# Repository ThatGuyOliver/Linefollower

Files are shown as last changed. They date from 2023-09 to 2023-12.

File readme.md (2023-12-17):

# LineFollower

A description of my image


## specifications

microcontroller:AZ-Delivery ESP32-WROOM-32

motors: Mini Micro Metal Gear Motor 6V 500TPM

h-bridge:Drv8833

sensors:QTR-8A

batteries:XTAR 2200mAh Li-ion battery

wireless communication: AZ-Delivery ESP32-WROOM-32

distance sensor - motors: 8,57 cm

weight: 260g

speed: 0.774 m/s

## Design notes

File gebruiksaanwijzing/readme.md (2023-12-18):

# Gebruiksaanwijzing

## opladen / vervangen batterijen
uitleg over het opladen of vervangen van de batterijen

### Opladen
Dit zijn li-ion batterijen van het type 18650.
Deze batterijen laad je best op voor en na een sessie.
Wanneer tijdens een sessie een verminderde prestatie wordt geleverd kan je dan ook best de batterijen opladen.
Voor het opladen van deze batterijen heb je een speciale lader nodig en wordt het ten zeerste afgeraden om een niet geschikte oplaadmethode te gebruiken.

### Vervangen batterijen
Zorg dat de batterijen in de correcte oriëntatie in de batterijhouder gestoken worden. En vergeet het deksel niet terug te plaatsen
Er wordt ook zeker aangeraden dat wanneer je deze batterijen vervangt, je ze afgeeft bij een geschikt inzamelings punt.

## draadloze communicatie
### verbinding maken
uitleg over het verbinden van de robot met laptop / smartphone
#### 1: Putty (op computer)
1.Verbind met hetzelde Wifi netwerk als de esp32
1.1. Het netwerk waarmee de esp32 wordt bepaald wordt bepaald in de main.cpp file.
2. Hostname: zelf gekozen hostname/ip esp32
2.1 Hostname wordt gekozen in main.cpp file
3. Port:  23
4. Connection type: Other: Telnet
#### 2: App IOS Termius
1.Verbind met hetzelde Wifi netwerk als de esp32
2. Navigeer naar Hosts tab
3. Klik op + in de linker hoek
4. New host
5. Hostname 
5.1 Hostname: zelf gekozen hostname 
6. Schakel Use SSH uit
7. Schakel Use Telnet aan
8. Save 
9. Klik nu op de net aangemaakte host

### commando's
#### debug Stuurt alle ingestelde parameters en berekende calculation time terug.
#### run Start of stopt de robot.
#### set cycle [µs]  Stelt de cycle time in van de robot.
#### set power [0..255] Stelt de maximum power van de robot in.
#### set diff [0..1] Stelt de verschil in power tussen de motoren in bochten
#### set kp [0..] Stelt de propertionele correctie van de fout in.
#### set ki [0..] Stelt de integrale correctie van de fout in.
#### set kd [0..] Stelt de differentiële correctie van de fout in.
#### calibrate black  Stelt de waardes gelezen door de sensor in als zwart.
#### calibrate white Stelt de waardes gelezen door de sensor in als wit.

## kalibratie
uitleg kalibratie  
Er moet worden gekalibreerd omdat er een verschil is tussen de verschillende sensoren, door een tolerantie op de onderdelen, wat eigen is aan productie.

Commando: calibrate black
Wanneer je dit commando stuurt over telnet wordt de reflectie van het opppervlakte waarover de sensor module op dat moment hangt opgeslagen
per sensor opgeslagen als een zwart waarde.
Commando: calibrate white
Wanneer je dit commando stuurt over telnet wordt de reflectie van het opppervlakte waarover de sensor module op dat moment hangt opgeslagen
per sensor opgeslagen als een wit waarde.

Deze waardes worden dan gebruikt om te vergelijken met de huidig gedetecteerd oppervlakte ofdat het een wit of zwart oppervlakte is.
Het is belangrijk dat je deze commandos opnieuw uitvoerd wanneer je van omgeving verandert zodat er correct kan gedetecteerd kan worden.

## settings
De robot rijdt stabiel met volgende parameters:  
#### cycle time: 2500
#### power: 80
#### Diff: 0.10
#### Kp: 30
#### Ki: 0
#### Kd: 1.00

## settings optimaal Plan A
#### cycle time: 200
#### power: 200
#### Diff: 0.01
#### Kp: 10
#### Ki: 0
#### Kd: 0.8

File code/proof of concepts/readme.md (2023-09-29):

# Proof of Concepts

Een proof of concept is een combinatie van minimale hard- en software om eenvoudig aan te tonen dat iets werkt.  
Proof of concepts kunnen enerzijds als eerste poging dienen om een bepaald onderdeel van het project werkend te krijgen. Anderzijds kunnen ze tijdens het debuggen van het finale project dienen als test om eventuele hardware problemen te elimineren bij onduidelijke problemen.
<br />  
<br />
Een proof of concept bestaat uit
* een elektronisch schema (indien van toepassing)
* minimale code om de voorop gestelde zaken te demonstreren
* minimale uitleg / aandachtspunten
<br />
De elektronische schakelingen van de proof of concepts komen bij voorkeur overeen met deze van de uiteindelijke linefollower, zodat de code zonder aanpassingen op het finale project kan draaien.

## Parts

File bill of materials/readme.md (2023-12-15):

## bill of materials plan B
<br />

|volgnummer|naam|omschrijving|nieuw/recup|kostprijs/stuk[€]|aantal|subtotaal[€]|
|---|----|---|---|---|---|---|
|1| Drv8833 H-Brug | Aliexpress 3-10V H-Brug | nieuw | 3,57|1|3,57|
|2|Breadboard| Aliexpress 400mm punten| nieuw|1,02|2|2,04|
|3|DC Motor| 6V DC, 50:1 ratio| nieuw | 2,04|2 |4,08|
|4|Achter Wiel| 40mm rubber wiel|nieuw|0,79|2|1,58|
|5|Batterij Houder| 2x18650 Batterij met switch|nieuw|0,32|1|0,32|
|6|Lijmpistool en patroon | HBM met 2 patronen | recup|2,99 | 1 |2,99|
|7|Reflectance sensor array |Polollulu QTR-8A|nieuw|10,39|1|10,39|
|7|Batterij lader|XTAR MC2 Plus batterijlader|nieuw|6,95|1|6,95|
|9|Batterij|XTAR 18650 2200mAh (protected) 5A|nieuw|4,45|2|8,90|
|10|ESP32 Microcontroller|AZ-Delivery ESP32-WROOM-32 NodeMCU Module|nieuw|7,60|1|7,60|
|11|Kabels|Meerkleurige kabels 0,75mm|nieuw|7|1|7|
|12|Voltage Regulator| +5V 1,5A L7805CV|0,75|1|0,75|
|13|Kogelwiel| Draaiende bal voor voorwiel|nieuw|1,10|1|1,10|
|14|Verbindings kabel| Micro USB voor connector ESP32|recup|*|1|*|
|15|Baseplate|Plaat waarop alles bevestigd wordt|nieuw|0,47|1|0,47|
|16|Motorhouders|Polulu motor houder|nieuw|0,06|2|0,12|
|17|Batterij Houder Platform| Verhoog voor montering battery houder|nieuw|0,58|1|0,58|
|18|Schroef|M3x12|recup|0,10|4|0,40|
|19|Moer|M3|recup|0,10|4|0,40|

## bill of materials plan A
<br />

|volgnummer|naam|omschrijving|nieuw/recup|kostprijs/stuk[€]|aantal|subtotaal[€]|
|---|----|---|---|---|---|---|
|1| Drv8833 H-Brug | Aliexpress 3-10V H-Brug | nieuw | 3,57|1|3,57|
|2|PCB Mainboard|Vervanging van breadboard|nieuw|2,63|1|2,63|
|3|DC Motor| 6V DC, 50:1 ratio| nieuw | 2,04|2 |4,08|
|4|Achter Wiel| 40mm rubber wiel|nieuw|0,79|2|1,58|
|5|Batterij Houder| 2x18650 Batterij met switch|nieuw|0,32|1|0,32|
|6|Lijmpistool en patroon | HBM met 2 patronen | recup|2,99 | 1 |2,99|
|7|Reflectance sensor array |Polollulu QTR-8A|nieuw|10,39|1|10,39|
|7|Batterij lader|XTAR MC2 Plus batterijlader|nieuw|6,95|1|6,95|
|9|Batterij|XTAR 18650 2200mAh (protected) 5A|nieuw|4,45|2|8,90|
|10|ESP32 Microcontroller|AZ-Delivery ESP32-WROOM-32 NodeMCU Module|nieuw|7,60|1|7,60|
|11|Kabels|Meerkleurige kabels 0,75mm|nieuw|7,00|1|7,00|
|12|Voltage Regulator| +5V 1,5A L7805CV|0,75|1|0,75|
|13|Kogelwiel| Draaiende bal voor voorwiel|nieuw|1,10|1|1,10|
|14|Verbindings kabel| Micro USB voor connector ESP32|recup|*|1|*|
|15|Baseplate|Plaat waarop alles bevestigd wordt|nieuw|0,47|1|0,47|
|16|Motorhouders|Polulu motor houder|nieuw|0,06|2|0,12|
|17|Batterij Houder Platform| Verhoog voor montering battery houder|nieuw|0,58|1|0,58|
|18|3 pin header f |Connector U-regulator|nieuw|0,12|1|0,12|
|19|20 pin header f| Connector esp32|nieuw|0,36|2|0,72|
|20|6 pin header f|Connector Drv8833 H-Brug|nieuw|0,18|2|0,36|
|21|12 pin header f|Connector Sensor|nieuw|0,28|1|0,28|
|22|4 pin Terminal Block| Terminal Block connector voor motoren|nieuw|0,45|1|0,45|
|23|2 pin Terminal Block| Terminal Block connector voor batterijen|nieuw|0,30|1|0,30|
|24|Schroef|M3x12|recup|0,10|4|0,40|
|25|Moer|M3|recup|0,10|4|0,40|

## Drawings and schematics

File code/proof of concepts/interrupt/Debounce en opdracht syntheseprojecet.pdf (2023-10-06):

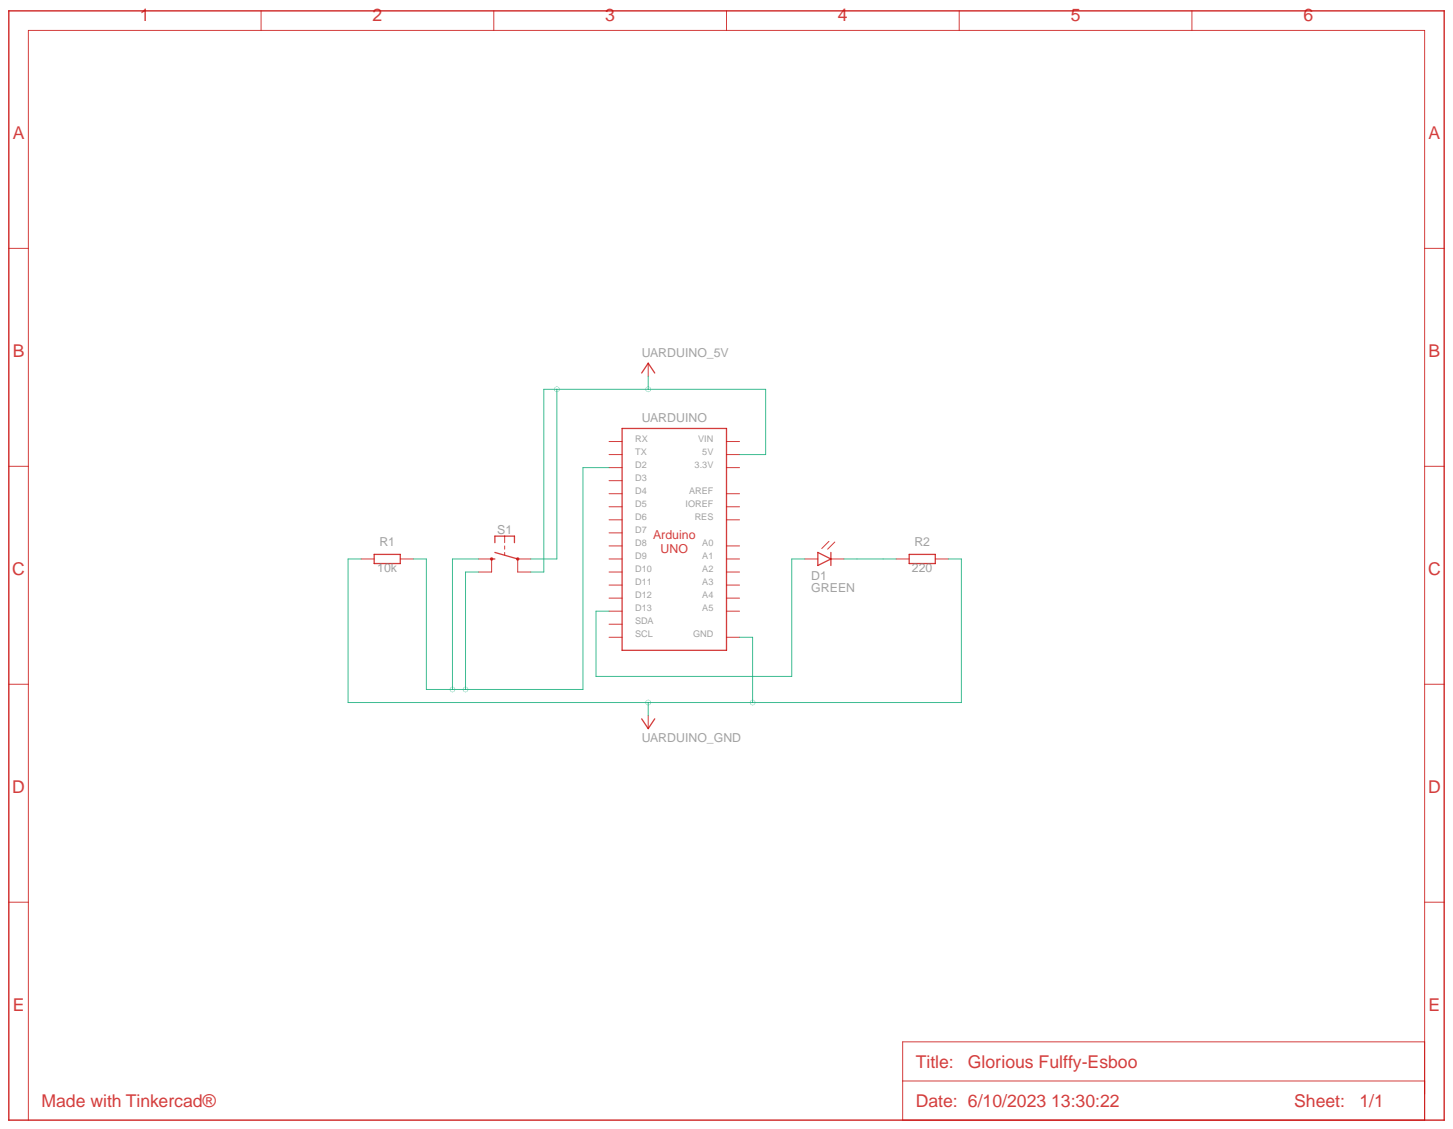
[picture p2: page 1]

Title: Glorious Fulffy-Esboo

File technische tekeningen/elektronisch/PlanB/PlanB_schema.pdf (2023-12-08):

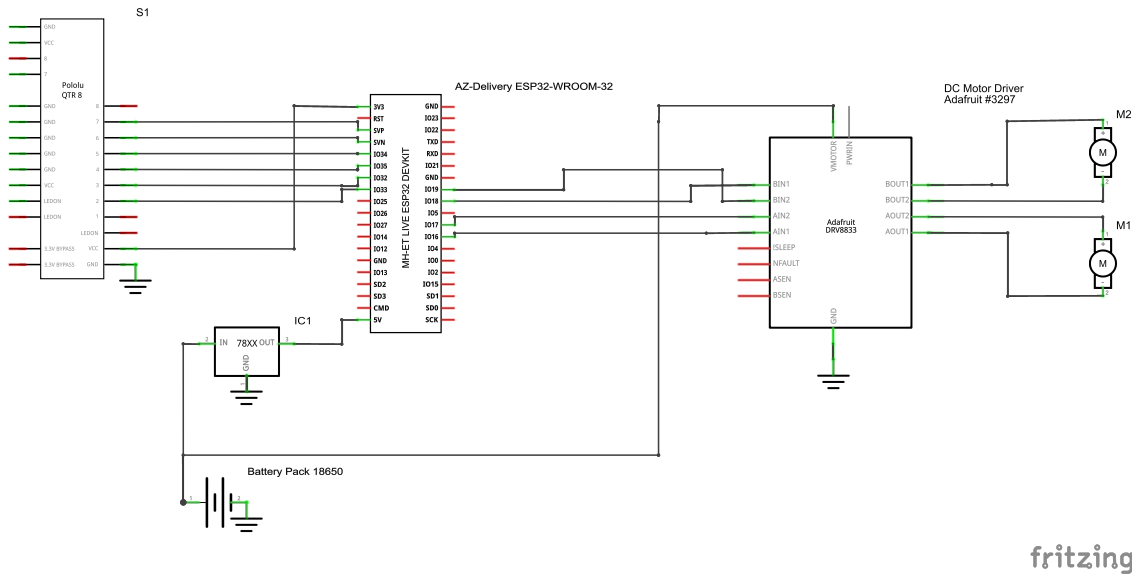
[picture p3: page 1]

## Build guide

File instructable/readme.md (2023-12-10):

# Instructable voor plan B

Een instructable is een stappenplan - zonder verdere uitleg - hoe je vertrekkend van de bill of materials en gebruik makend van de technische tekeningen de robot kan nabouwen. Ook de nodige stappen om de microcontroller te compileren en te uploaden staan beschreven.  

## stap 1
Bestel alle componenten uit de bill of materials  
## stap 2
Leg de breadboards in de lengte naast elkaar.
## stap 3
Maak de zijstukken los, maar behoud één zijstuk op één breadboard.
## stap 4
Nu moet je een configuratie verkrijgen van breadboards zoals volgt: Groot Breadboard - Klein Breadboard - Groot Breadboard. Hang deze breadboards aan elkaar.
## stap 5
Verwijder de gele sticker aan de onderkant van het breadboard, zodat de onderkant plakkerig wordt.
## stap 6
Plak dit breadboard nu op de baseplate tussen de verhogingen en vlak met de achterkant van de baseplate (Niet bij de uitsteeksels).
## stap 7
Knip de uitsteeksels af totdat er nog 4 gaten overblijven op elk uitsteeksel.
## stap 8
Soldeer de draadjes aan de motoren (eventueel knip je een draad in twee).
## stap 9
Lijm de motorhouders nu vast zodat de palmbomen naar buiten wijzen en ze in hun respectieve hoek zitten, dus aan de linker en rechter achterhoek.
### stap 10
Soldeer de pin headers van de sensor in de rij met 11 gaten naast elkaar, met het lange stuk naar boven (het vlak zonder de componenten).
## stap 11
Soldeer de header van de H-brug met de lange kant naar beneden (lange kant naar de kant zonder componenten).
## stap 12
Bevestig de sensor module met behulp van lijm aan de onderkant van het uitsteeksel op het tweede gaatje. Zorg ervoor dat het lange deel van de headers naar boven steekt en de sensoren naar beneden wijzen.
## stap 13
Bevestig het kogelwiel in het midden van de robot, zodat het de sensor net niet raakt.
### stap 14
Duw de wielen op de motoren.
## stap 15
Duw de motoren in de motorenhouders (op een naar buiten wijzende manier) totdat alleen nog het "gouden" gedeelte van de motor uitsteekt.
## stap 16
!Vanaf nu is het perspectief vanuit de achterkant van de robot.!
Plaats de ESP32 met de micro USB naar achteren tegen de rand en over het kleine breadboard, zodat de linker pins zich op het linker breadboard bevinden en de rechter pins op het rechter breadboard.
## stap 17
Plaats de voltage regulator in de lengte, links van de ESP32, op de linker helft van het linker breadboard.
## stap 18
Plaats de H-Brug in de rechter bovenhoek, met de lange kant van de headers in het breadboard. Zorg ervoor dat hij over de gleuf staat, zodat de twee kanten niet op hetzelfde deel staan.
## stap 19
Bevestig de batterijhouder aan het Batterij Houder Platform met behulp van de schroefjes en moeren. Plaats de batterijhouder zodat de draadjes aan de linkerkant terechtkomen in de volgende stap.
## stap 20
Schuif de Batterij Houder Platform via de voorkant tot het vlak is met het baseplate deel.
## stap 21
Verbind nu alle draden volgens het elektrisch schema:
https://github.com/ThatGuyOliver/Linefollower/blob/main/technische%20tekeningen/elektronisch/PlanB/PlanB_schema.pdf
Je kan eventueel plakband gebruiken als de kabels niet goed zijn.
## stap 22
Eventueel laad je de batterijen op.
## stap 23
Zet de schakelaar van de batterijhouder op "OFF".
## stap 24
Installeer Visual Studio Code op je computer.
https://code.visualstudio.com/download
## stap 25
Wanneer je op het startscherm bent, klik je in de linkerbalk op extensions.
## stap 26
Zoek naar en installeer Platform IO.
## stap 27
Nu klik je op de alien en wordt Platform IO gestart. Hierna herlaad je Visual Studio.
## stap 28
Download deze zip en unzip naar een bereikbare locatie.
https://github.com/ThatGuyOliver/Linefollower/blob/main/code/finaal/Line%20Follower.zip
## stap 29
In Visual Studio klik je op de Alien op de linker tab en daarna op open project. 
Selecteer de map met de bestanden die je net hebt uitgepakt. Wacht tot het project is ingeladen.
## stap 30
In de explorer tab klik je de folder src open.
## stap 31
Klik vervolgens op main.cpp.
## stap 32
In deze file zoek je naar de parameters SSID, PSWD en MyHostName.
## stap 33
!Bij deze parameters pas je alleen de tekst tussen de "aanhalingstekens" aan!
De SSID naar de naam van je WIFI netwerk, PSWD naar het wachtwoord van je Wifi netwerk en Myhostname naar iets van jouw voorkeur.
## stap 34
Nu verbind je de ESP32 met je computer door de kabel in de USB micro te verbinden met een USB-poort van de computer waarop Visual Studio staat.
## stap 35
Je download en unzipt https://github.com/ThatGuyOliver/Linefollower/blob/main/instructable/CP210x_Universal_Windows_Driver.zip
Dit is de driver voor de esp32.
## stap 36
Nu installeer je deze driver, dit is afhankelijk van platform tot platform.
## stap 37
Na een succesvolle installatie herstart je best Visual Studio Code en sluit je de ESP32 opnieuw aan.
## stap 38
Keer terug naar het project.
## stap 39
Laad het programma op de ESP32 door op 'upload' te klikken (dit is een knop op de onderste balk, de pijl naar rechts).
## stap 40
Na een succesvolle upload open je de serial monitor, dit is het symbool met de stekker.
## stap 41
Wanneer je alles correct hebt gedaan, zou hier na enkele seconden het IP van je ESP32 verschijnen. !Noteer dit.!
## stap 42
Nu trek je de kabel uit de ESP32.
## stap 43
Plaats de batterijen in de batterijhouder.
Als deze nog niet open is, dan schuif je er eerst het deksel eraf. 
## stap 44
Schuif het deksel er weer op.
## stap 45
Zet de schakelaar van de batterijhouder op 'ON'.

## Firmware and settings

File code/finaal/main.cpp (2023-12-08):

#include <Arduino.h>
#include <WiFi.h>
#include <EEPROM.h>
#include "TelnetCommand.h"
#include "TelnetCommand.cpp"

#define SerialPort Serial
#define Baudrate 115200

//Wifi Login;
const char* ssid = "HGDevice";
const char* pswd = "KillAllHuman$";
const char* MyHostName = "LinefollowerOliver";
int port = 23;

WiFiServer telnetServer(port);
WiFiClient client;
TelnetCommand telnetCmd(SerialPort);

//Motor
#define MotorLeftForward 16
#define MotorLeftBackward 17
#define MotorRightForward 18
#define MotorRightBackward 19

//Void function
void onUnknownCommand(char *command);
void onSet();
void onDebug();
void onCalibrate();
void onRun();
void mainLoop();

//Sensoren
const int sensor[] = {36, 39, 34, 35, 32, 33};
//const int sensor[] = {33, 32, 35, 34, 39, 36};
struct param_t
{
  unsigned long cycleTime;
  uint black[6];
  uint white[6];
  uint power;
  float diff;
  float kp;
  float ki;
  float kd;

  /* andere parameters die in het eeprom geheugen moeten opgeslagen worden voeg je hier toe ... */
} params;
#define EEPROM_SIZE sizeof(param_t)


//Globalised Variables
int normalised[6];
float debugPosition;
bool debug;
bool run;
unsigned long previous, calculationTime;
float iTerm;
float lastErr;

void setup()
{
  SerialPort.begin(Baudrate);

  //Regelen 
  iTerm = 0;
  
  //EEPROM
  EEPROM.begin(EEPROM_SIZE);
  EEPROM.get(0, params);
  EEPROM.end();

  SerialPort.println("Welcome to ESP32 Serial:");
  run = false;
  //Wifi 
  
  WiFi.setHostname(MyHostName);
  WiFi.begin(ssid, pswd);
  while (WiFi.status() != WL_CONNECTED) 
  {
    delay(1000);
    SerialPort.println("Connecting to WiFi...");
  }

  SerialPort.println("Connected to WiFi");
  SerialPort.print("IP address: ");
  SerialPort.println(WiFi.localIP());

  telnetServer.begin();
  SerialPort.print("Port: ");
  SerialPort.println(port);

  telnetCmd.addCommand("set", onSet);
  telnetCmd.addCommand("debug", onDebug);
  telnetCmd.addCommand("calibrate", onCalibrate);
  telnetCmd.addCommand("run", onRun);
  telnetCmd.setDefaultHandler(onUnknownCommand);
}

void loop()
{
  //Wifi
  client = telnetServer.available();
  telnetCmd.readStream(client);
  if (client) 
  {
    Serial.println("New Telnet client connected");
    client.println("Welcome to ESP32-Robot Telnet Server");
    while (client.connected()) 
    {
      if (client.available()) {telnetCmd.readStream(client);}
      mainLoop();
    }
    Serial.println("Telnet client disconnected");
  }
}
void mainLoop()
{
  //Main Loop
  unsigned long current = micros();
  if (current - previous >= params.cycleTime)
  {
    previous = current;
    
    //sensoren
    for(int i=0;i<6;i++) normalised[i] = map(analogRead(sensor[i]), params.black[i], params.white[i], 0, 4096);
    
    float position = 0;

    //positie zwartste sensor 
    int index = 0;
    for (int i = 1; i < 6; i++) if (normalised[i] < normalised[index]) index = i;

    if (normalised[index] > 3000) run = false;
    
    //Is indix op de rand 
    if (index == 0) position = -50;
    else if (index == 7) position = 50;
    else
    {
    
    //waarde toekennen aan de 3 punten voor interpolatie
    long sNul = normalised[index];
    long sMinEen = normalised[index-1];
    long sPlusEen = normalised[index+1];
    //berekenen punten
    float b = ((float) (sPlusEen - sMinEen)) / 2;
    float a = sPlusEen - b - sNul;

    position = -b / (2 * a);  
    //Verschuiven y as
    position += index - 3.5;   
    position *= 15;
    }
    debugPosition = position;

    float error = -position;

    //Proportioneel
    float output = error * params.kp;
    
    //Integrerend
    iTerm += params.ki * error;
    iTerm = constrain(iTerm, -510, 510);
    output += iTerm;

    //Differentieel
    output += params.kd * (error - lastErr);
    lastErr = error;

    output = constrain(output, -510, 510);
    int powerLeft =0;
    int powerRight = 0;
    
    if (run) if (output >= 0)
    {
      powerLeft = constrain(params.power + params.diff * output, -255, 255);
      powerRight = constrain(powerLeft - output, -255, 255);
     powerLeft = powerRight + output;
    }
    else
    {
      powerRight = constrain(params.power - params.diff * output, -255, 255);
      powerLeft = constrain(powerRight + output, -255, 255);
      powerRight = powerLeft - output;
    }
    analogWrite(MotorLeftForward, powerLeft > 0 ? powerLeft : 0);
    analogWrite(MotorLeftBackward, powerLeft < 0 ? -powerLeft : 0);
    analogWrite(MotorRightForward, powerRight > 0 ? powerRight : 0);
    analogWrite(MotorRightBackward, powerRight < 0 ? -powerRight : 0);
  }
  unsigned long difference = micros() - current;
  if (difference > calculationTime) calculationTime = difference;
}

void onUnknownCommand(char *command)
{
  client.print("unknown command: \"");
  client.print(command);
  client.println("\"");
}

void onSet()
{  
  char* param = telnetCmd.next();
  char* value = telnetCmd.next();

  /*
  if (strcmp(param, "debug") == 0)
  {
    if (strcmp(value, "on") == 0) debug = true;
    else if (strcmp(value, "off") == 0) debug = false;
  }
  */
 /*
 else  if (strcmp(param, "cycle") == 0) 
  {
    long newCycleTime = atol(value);
    float ratio = ((float) newCycleTime) / ((float) params.cycleTime);
    params.cycleTime = newCycleTime;
    SerialPort.print("New cycle time: ");
    SerialPort.println(params.cycleTime);
  }
  */
  if (strcmp(param, "cycle") == 0)
  {
    long newCycleTime = atol(value);
    float ratio = ((float) newCycleTime) / ((float) params.cycleTime);

    params.ki *= ratio;
    params.kd /= ratio;

    params.cycleTime = newCycleTime;
  } 
  else if (strcmp(param, "power") == 0) params.power = atol(value);
  else if (strcmp(param, "diff") == 0) params.diff = atof(value);
  else if (strcmp(param, "kp") == 0) params.kp = atof(value);
  else if (strcmp(param, "ki") == 0) params.ki = atof(value) * (((float) params.cycleTime) / 1000000);
  else if (strcmp(param, "kd") == 0) params.kd = atof(value) / (((float) params.cycleTime) / 1000000);

  EEPROM.begin(EEPROM_SIZE);
  EEPROM.put(0, params);
  EEPROM.commit();
  EEPROM.end();
}
void onDebug()
{
  client.print("cycle time: ");
  client.println(params.cycleTime);
  
  /* parameters weergeven met behulp van het debug commando doe je hier ... */
  client.print("black: ");
  for (int i =0; i <6; i++)
  {
    client.print(params.black[i]);
    client.print(" ");
  }
  client.println(" ");
 
 client.print("white: ");
  for (int i =0; i <6; i++)
  {
    client.print(params.white[i]);
    client.print(" ");
  }
  client.println(" ");
 
 client.print("normalised: ");
  for (int i =0; i <6; i++)
  {
    client.print(normalised[i]);
    client.print(" ");
  }
  client.println(" ");

  client.print("position: ");
  client.println(debugPosition);
  /*for (int i =0; i <6; i++)
  {
    SerialPort.print(debugPosition);
    SerialPort.print(" ");
  }
  */

  client.print("Power: ");
  client.println(params.power);
  client.print("Diff: ");
  client.println(params.diff);
  client.print("Kp: ");
  client.println(params.kp);
  client.print("Ki: ");
  client.println(params.ki /(((float) params.cycleTime )/ 1000000));
  client.print("Kd: ");
  client.println(params.kd *(((float) params.cycleTime) / 1000000));

  client.print("Run state: ");
  client.println(run);

  client.print("calculation time: ");
  client.println(calculationTime);
  calculationTime = 0;
}

void onCalibrate()
{
  char* param = telnetCmd.next();

  if (strcmp(param, "black") == 0)
  {
    client.print("start calibrating black... ");
    for (int i = 0; i < 6; i++) params.black[i]=analogRead(sensor[i]);
    client.println("done");
  }
  else if (strcmp(param, "white") == 0)
  {
    client.print("start calibrating white... ");    
    for (int i = 0; i < 6; i++) params.white[i]=analogRead(sensor[i]);  
    client.println("done");      
  }

  EEPROM.begin(EEPROM_SIZE);
  EEPROM.put(0, params);
  EEPROM.commit();
  EEPROM.end();
}

void onRun()
{
  if (run == false) 
  {
    iTerm = 0;
    run = true;
  }
  else run = false;
}

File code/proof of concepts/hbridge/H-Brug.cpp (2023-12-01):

#include <Arduino.h>

#define SerialPort Serial
#define Baudrate 115200

//Pins Instellen
const int motor1PWM1 = 16;  //PWM pin for motor 1 driver input 1
const int motor1PWM2 = 17;  //PWM pin for motor 1 driver input 2
const int motor2PWM1 = 18;  //PWM pin for motor 2 driver input 1
const int motor2PWM2 = 19;  //PWM pin for motor 2 driver input 2
const int delayTime = 25;   //Delay in milliseconds between each step


void motor1CW();
void motor1CCW();
void motor2CW();
void motor2CCW();
void samenC();

void setup() 
{
  //Seriële Poort
  SerialPort.begin(Baudrate);
  delay(100);

  pinMode(motor1PWM1, OUTPUT);
  pinMode(motor1PWM2, OUTPUT);
  pinMode(motor2PWM1, OUTPUT);
  pinMode(motor2PWM2, OUTPUT);
}

void loop() 
{   
  if (Serial.available()) { 
    String command = Serial.readStringUntil('\n');

    if (command == "M1") {
      Serial.println("Motor 1 Clockwise");
      motor1CW();
    } 
    else if (command == "O2") {

      Serial.println("Motor 2 Clockwise");
      motor2CW();
    } 
    else if (command == "A1") {

      Serial.println("Motor 1 Counterclockwise");
      motor1CCW();
    } 
    else if (command == "B2") {

      Serial.println("Motor 2 Counterclockwise");
      motor2CCW();
    }
    else if (command == "SA") {

      Serial.println("Motoren Werken Samen Clockwise");
      samenC();
    }
  }
}


void motor1CW()
{
  for (int speed = 40; speed <= 125; speed++)
  {
    analogWrite(motor1PWM1, 0);
    analogWrite(motor1PWM2, speed);
    delay(delayTime);
  }
  for (int speed = 125; speed >= 30; speed--) 
  {
    analogWrite(motor1PWM1, 0);
    analogWrite(motor1PWM2, speed);
    delay(delayTime);
  }
}

void motor2CW()
{
  for (int speed = 40; speed <= 125; speed++)
  {
    analogWrite(motor2PWM1, 0);
    analogWrite(motor2PWM2, speed);
    delay(delayTime);
  }
  for (int speed = 125; speed >= 30; speed--) 
  {
    analogWrite(motor2PWM1, 0);
    analogWrite(motor2PWM2, speed);
    delay(delayTime);
  }
}

void motor1CCW()
{
  for (int speed = 40; speed <= 125; speed++)
  {
    analogWrite(motor1PWM1, speed);
    analogWrite(motor1PWM2, 0);
    delay(delayTime);
  }
  for (int speed = 125; speed >= 30; speed--) 
  {
    analogWrite(motor1PWM1, speed);
    analogWrite(motor1PWM2, 0);
    delay(delayTime);
  }
}

void motor2CCW()
{
  for (int speed = 40; speed <= 125; speed++)
  {
    analogWrite(motor2PWM1, speed);
    analogWrite(motor2PWM2, 0);
    delay(delayTime);
  }
  for (int speed = 125; speed >= 30; speed--) 
  {
    analogWrite(motor2PWM1, speed);
    analogWrite(motor2PWM2, 0);
    delay(delayTime);
  }
}

void samenC()
{
  for (int speed = 40; speed <= 125; speed++)
  {
    analogWrite(motor1PWM1, 0);
    analogWrite(motor1PWM2, speed);
    analogWrite(motor2PWM1, 0);
    analogWrite(motor2PWM2, speed);
    delay(delayTime);
  }
  for (int speed = 125; speed >= 30; speed--) 
  {
    analogWrite(motor1PWM1, 0);
    analogWrite(motor1PWM2, speed);
    analogWrite(motor2PWM1, 0);
    analogWrite(motor2PWM2, speed);
    delay(delayTime);
  }
}
